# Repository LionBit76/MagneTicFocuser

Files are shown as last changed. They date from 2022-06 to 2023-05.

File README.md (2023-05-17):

# MagneTicFocuser [MTF]
DIY focuser for astrophotography with a magnetic flange

My Blogpost with more details (german): https://astrophoto.lionbit.com/3d-druck/22-magneticfocuser

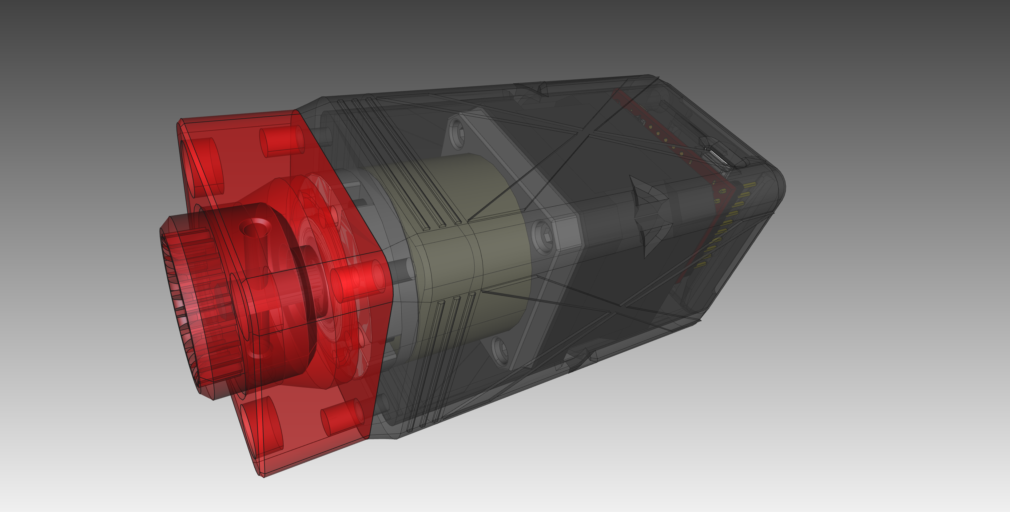
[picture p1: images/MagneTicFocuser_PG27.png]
This is an image


When I was looking for a cheap way to get a focuser, I came across a project on GitHub called TicFocuser-NG. This is an INDI driver for a Pololu TIC Controller. This controller is a small, compact circuit board with a stepper motor driver and a controller that is addressed via MicroUSB. The advantage of this solution is that you don't need an Arduino or Raspberry Pi to control the stepper motor driver, everything is on a board that is smaller than the area of a NEMA17 motor.

This focuser is for astrophotography with the INDI driver TicFocuser-ng https://github.com/sebo-b/TicFocuser-ng

### BOM [MagneTicFocuser]:

- 1x STEPPERONLINE 17HS13-0404S-PG27 
- 1x Pololu Tic T500 
- 4x M3x6 for fastening the geared motor 
- 4x M3x10 for the connection between housing and magnet plate
- 2x M2x8 self-tapping for attaching the controller
- 2x M4x10 grub screw for the clutch
- 4 N45 neodymium magnets 9x5 (4 more for the flange on the telescope)
- 1x barrel connector socket 5.5x2.1 for 12V DC
- 4x heatset inserts M3 5x6 (I have the VORON compatible heatset inserts)
- Superglue to stick the magnets in place
- JST connectors 4-pin for stepper, 2-pin for 12v

### Motor settings:
My settings in the Tic Software for the stepper motor are:
- Current limit: 1mA (yes, it works!)
- Step mode: 1/8 step (for maximum resolution and less vibrations on accel/deccel)
- Max speed: 8000000
- Max accel: 80000

### MagneTicFocuser and Explore Scientific ED80:
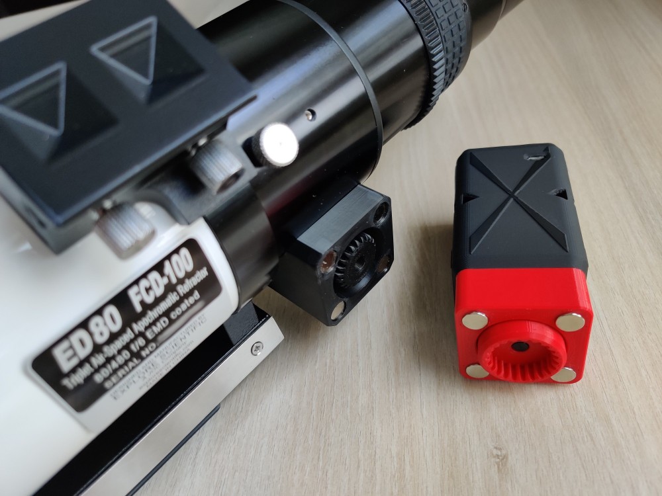
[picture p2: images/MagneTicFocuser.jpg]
This is an image


### MagneTicFocuser mounted on Explore Scientific ED80:
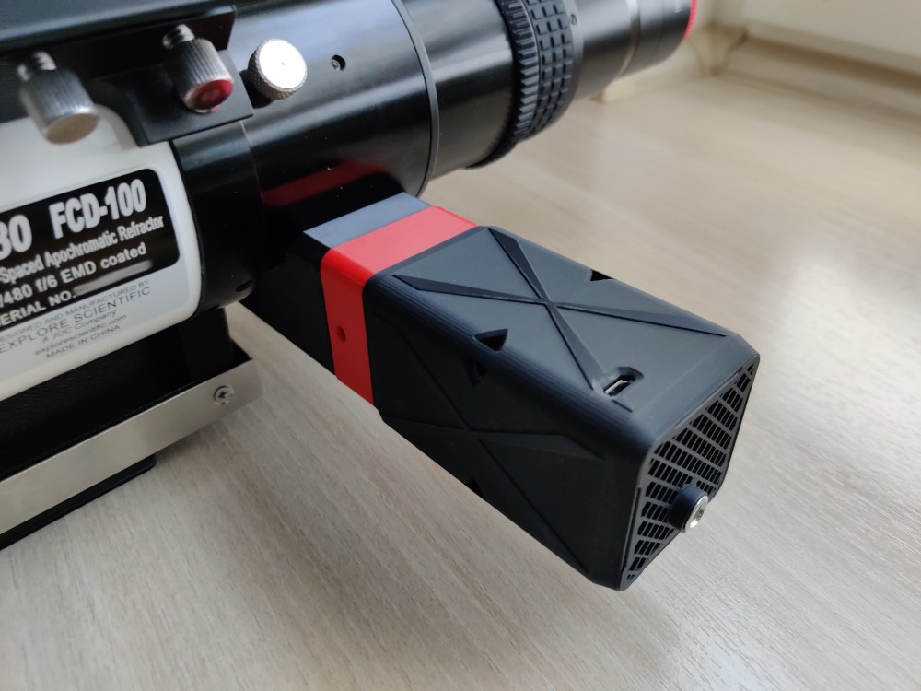
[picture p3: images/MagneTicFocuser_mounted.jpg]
This is an image


### MagneTicFocuser mounted on a Newton with Baader BDS-NT Focuser:
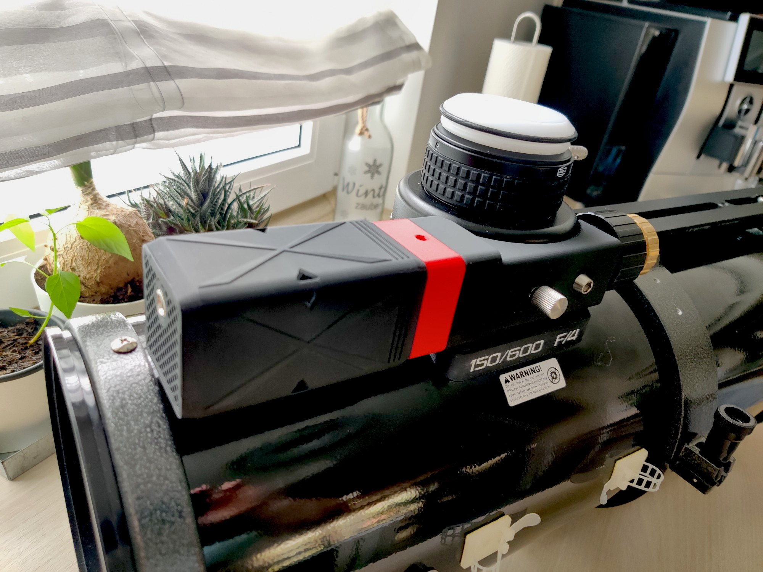
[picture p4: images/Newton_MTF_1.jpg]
This is an image

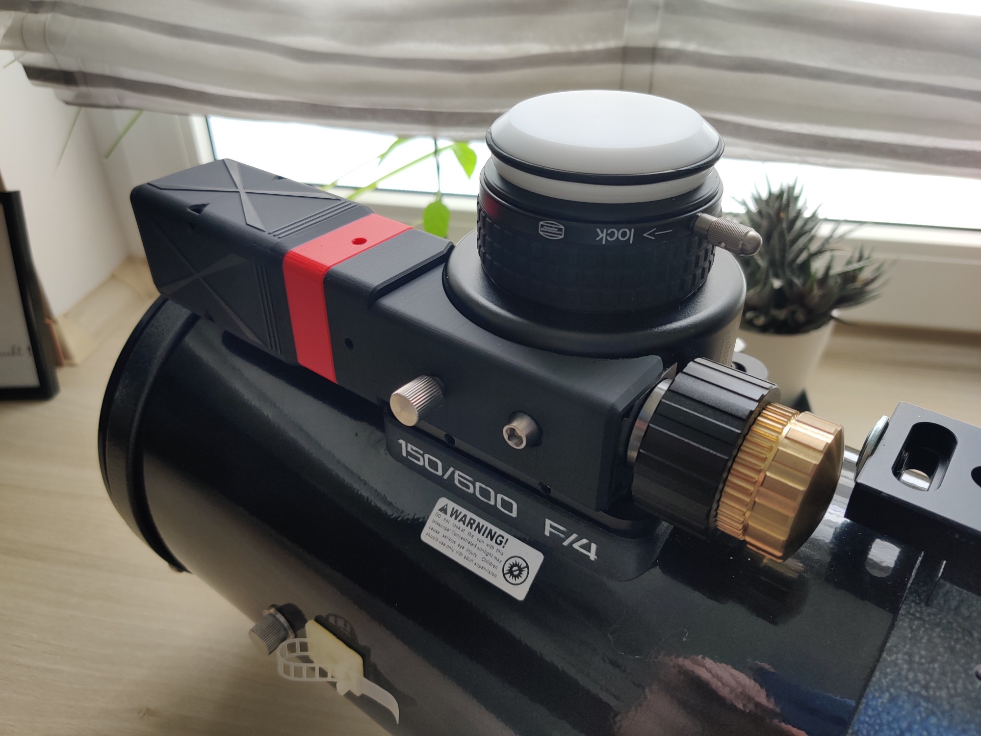
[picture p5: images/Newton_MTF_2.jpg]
This is an image


### My Rig:
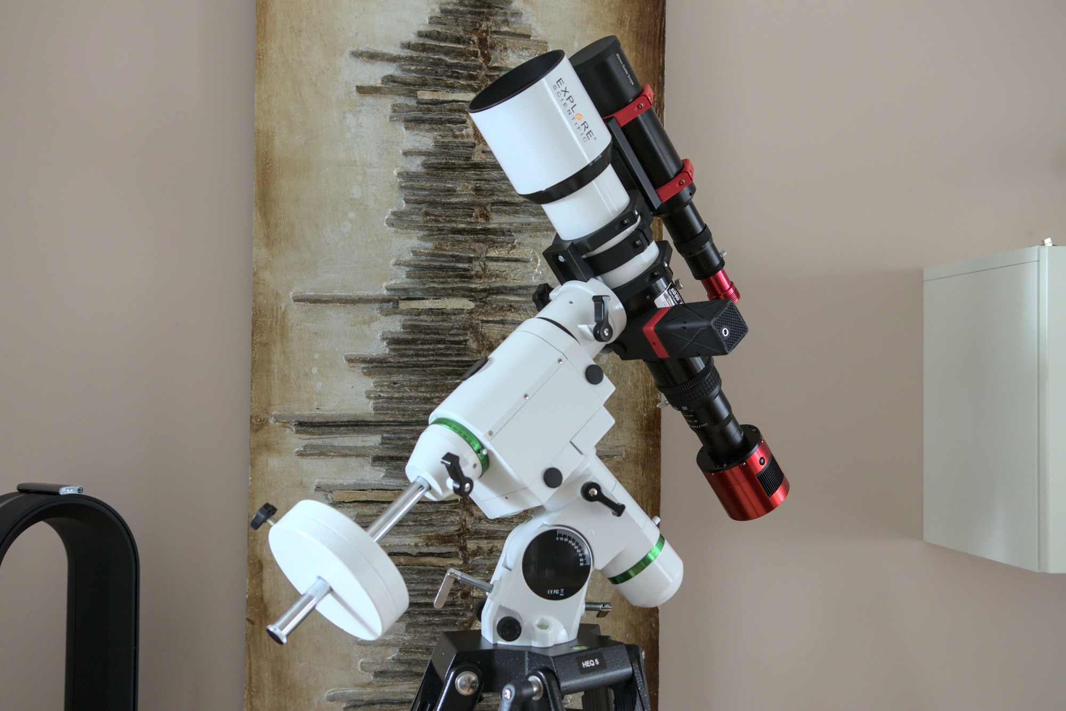
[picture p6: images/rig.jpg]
This is an image


### MTF to EAF Adapter:
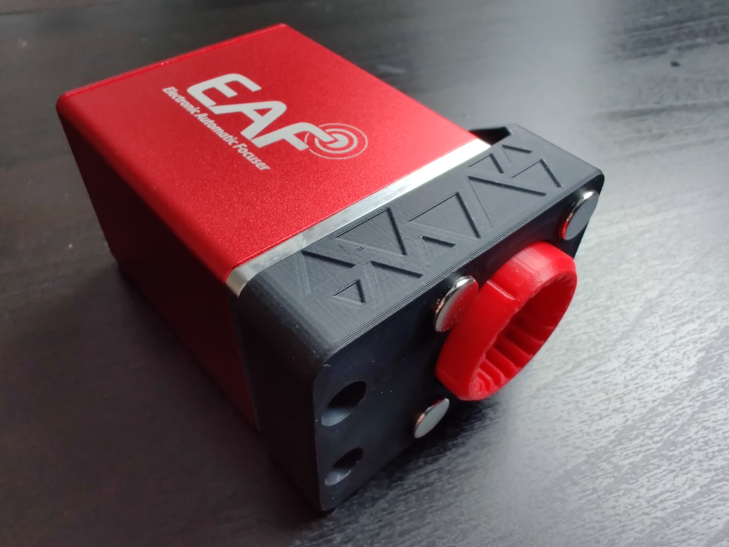
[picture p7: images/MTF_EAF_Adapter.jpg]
This is an image

If you have an ZWO EAF, you can adapt it to the MTF (MagneTicFocuser) System

### How to mount:
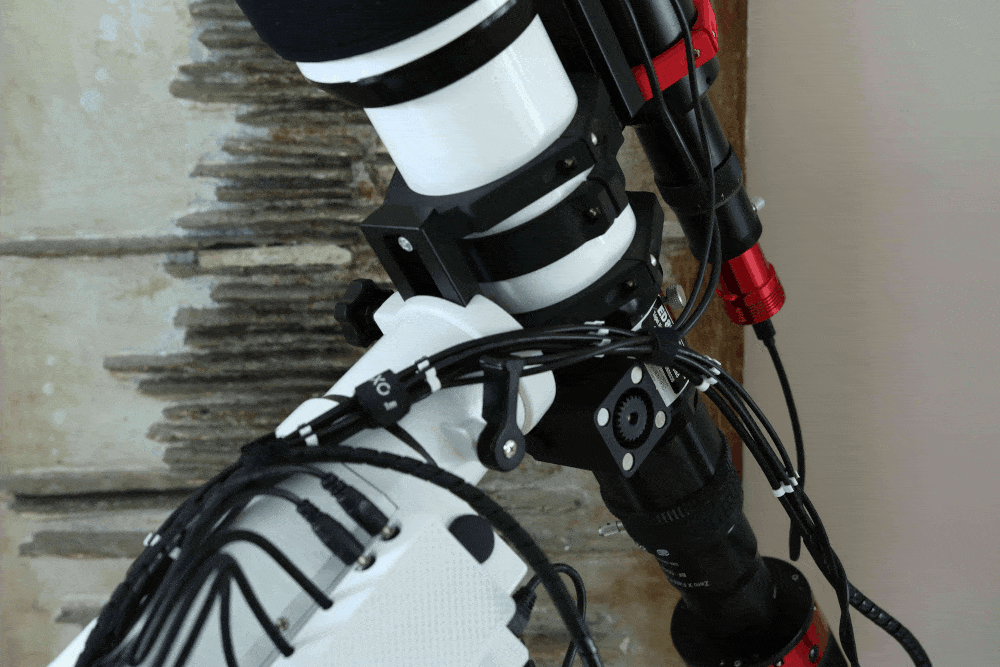
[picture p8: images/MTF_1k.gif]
This is an image


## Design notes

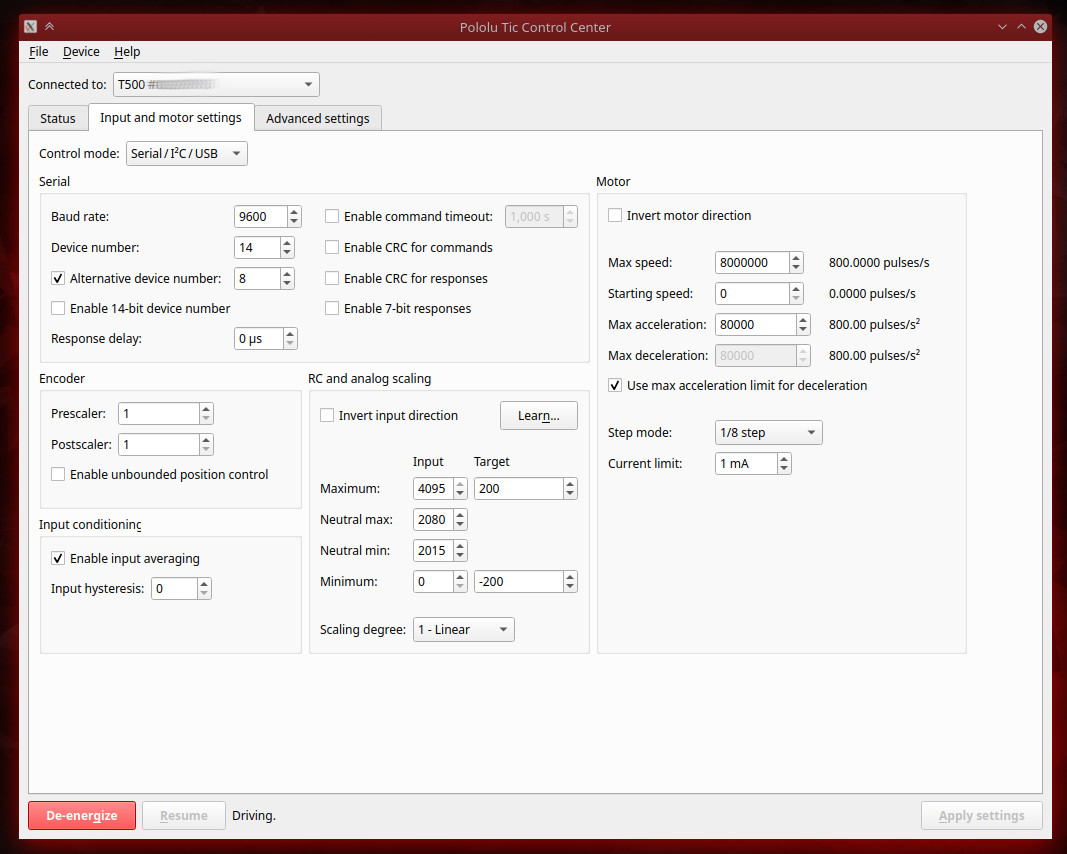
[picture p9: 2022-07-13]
images/TicGUI_Tab_InputMotorSetting.jpg

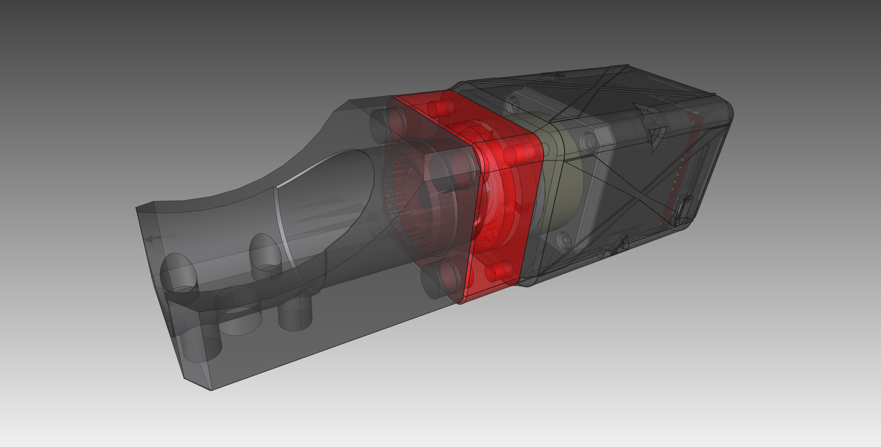
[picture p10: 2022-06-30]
images/MagneTicFocuser_ES_FCD100.png

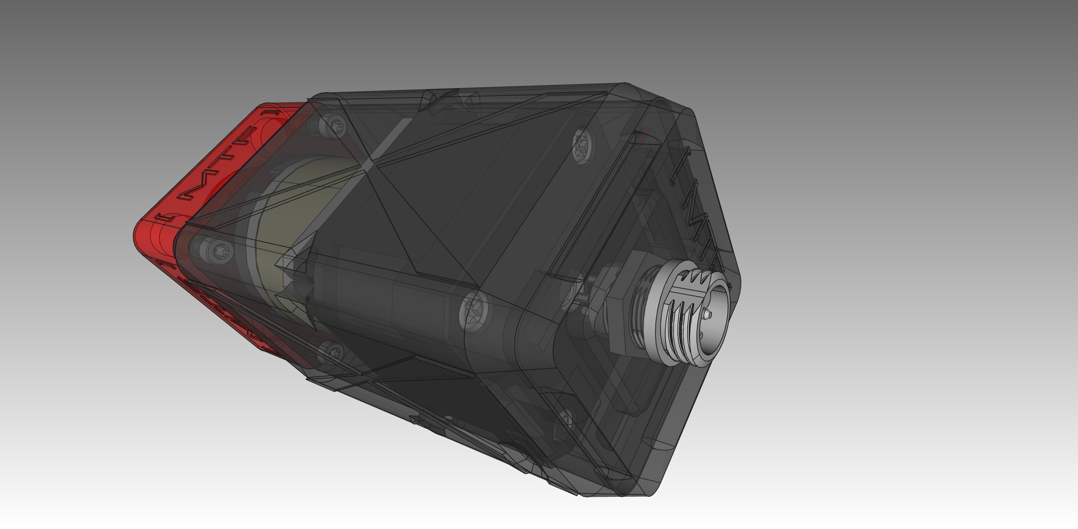
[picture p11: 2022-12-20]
STL/MTF-GX12/MTF_GX12_Back.png

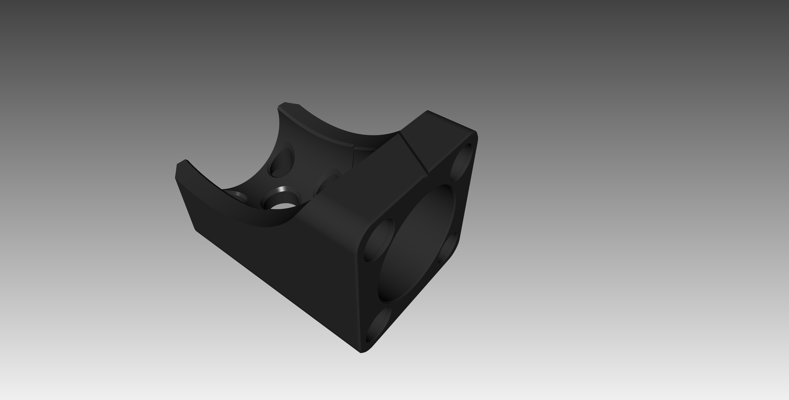
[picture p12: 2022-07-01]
STL/Telescope_Flange/Hexafoc/MTF_Hexafoc.png

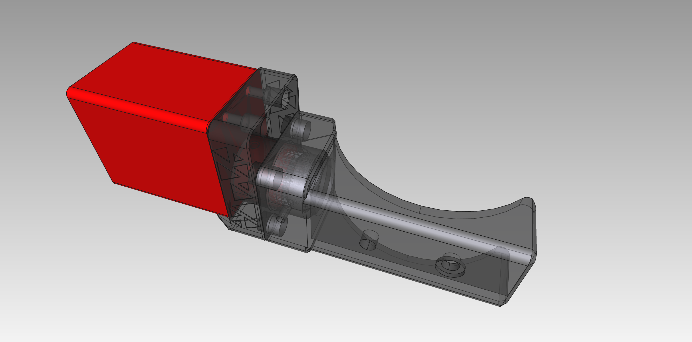
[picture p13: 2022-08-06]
STL/MTF_EAF/EAF_Adapter.png

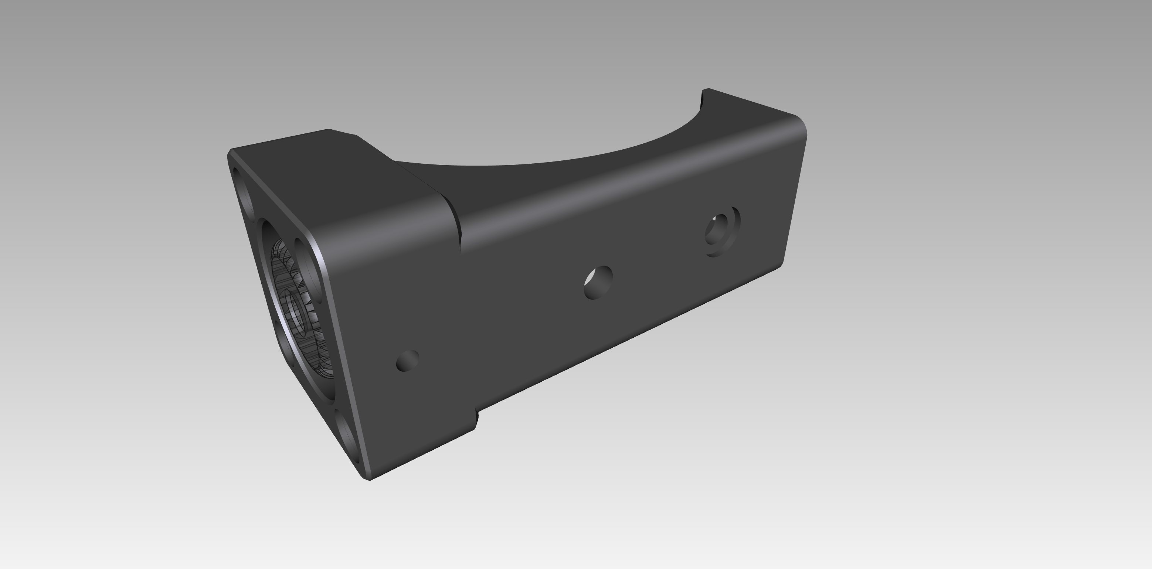
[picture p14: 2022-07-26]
STL/Telescope_Flange/Baader_BDS/MTF_BAADER_BDS.png

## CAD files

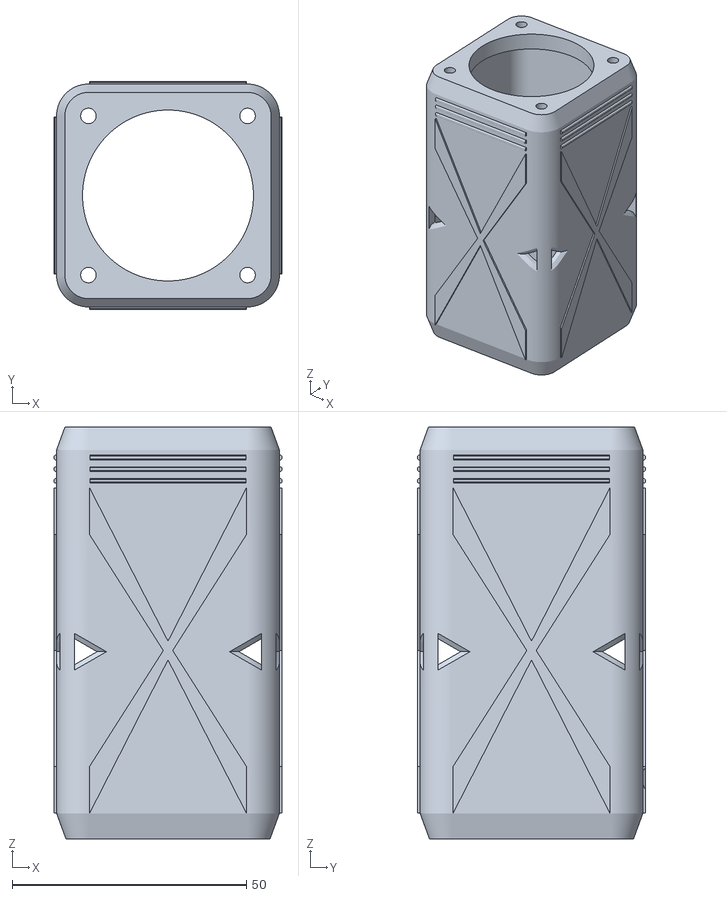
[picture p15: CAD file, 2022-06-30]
STL/MagneTicFocuser/MTF_Housing.stl
48.6 x 48.6 x 88.0

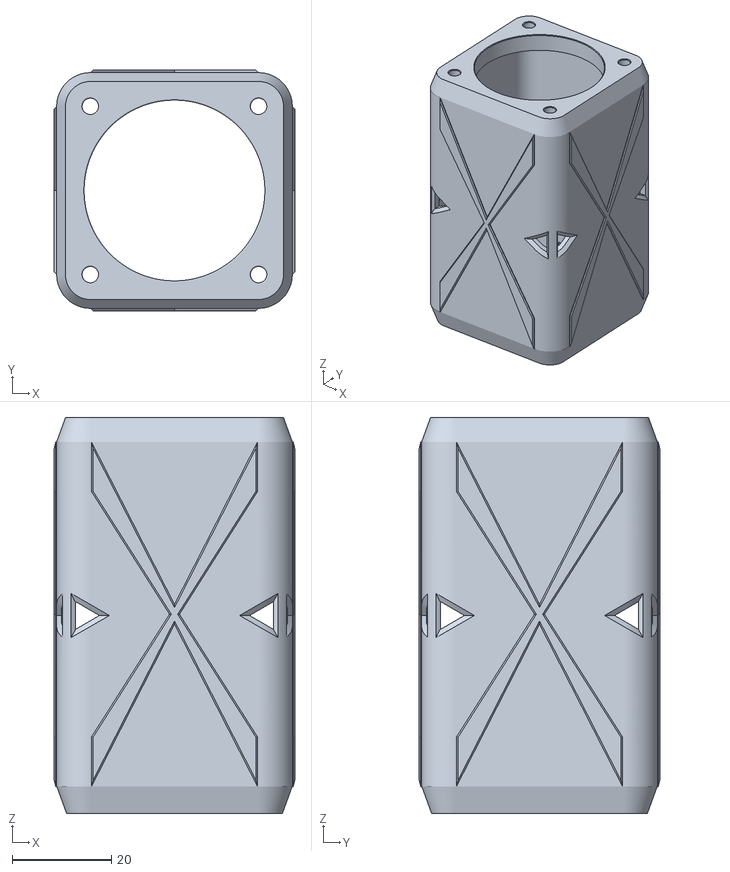
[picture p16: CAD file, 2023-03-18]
STL/MTF-GX12/MTF_Housing_PG5_GX12.stl
48.6 x 48.6 x 80.0

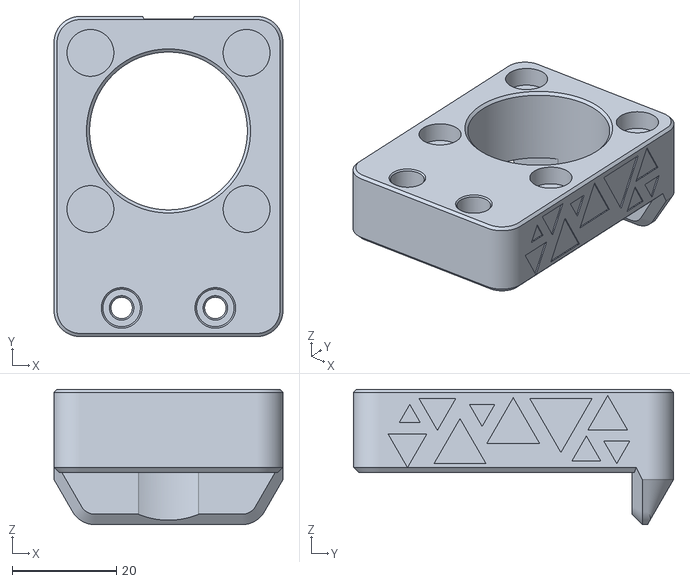
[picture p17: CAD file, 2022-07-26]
STL/MTF_EAF/EAF_Adapter.stl
44.0 x 61.5 x 26.0

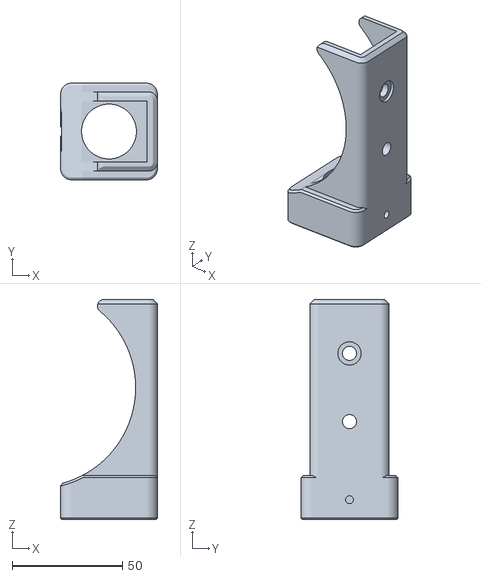
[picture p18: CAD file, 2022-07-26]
STL/Telescope_Flange/Baader_BDS/MTF_BAADER_BDS.stl
44.0 x 44.0 x 100.0

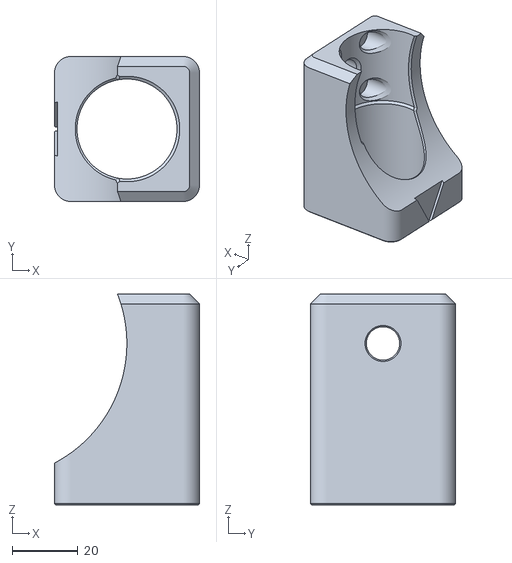
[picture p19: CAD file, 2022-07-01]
STL/Telescope_Flange/Hexafoc/MTF_Hexafoc.stl
44.0 x 44.0 x 64.0

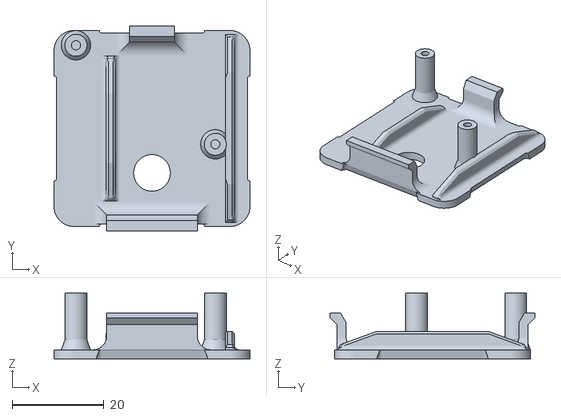
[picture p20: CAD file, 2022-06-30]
STL/MagneTicFocuser/MTF_Cover.stl
42.8 x 44.8 x 14.4

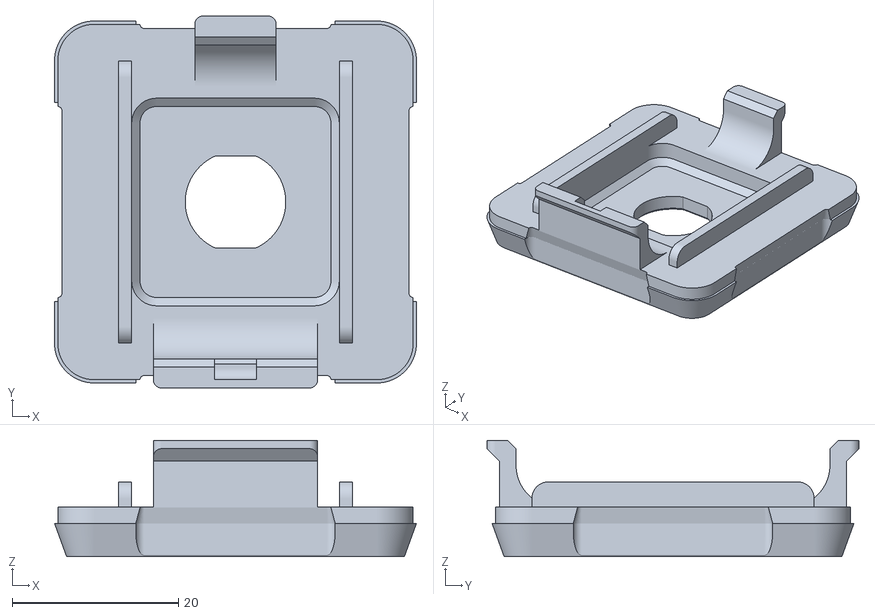
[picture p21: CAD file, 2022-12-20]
STL/MTF-GX12/MTF_Cover_GX12.stl
43.6 x 44.8 x 14.0

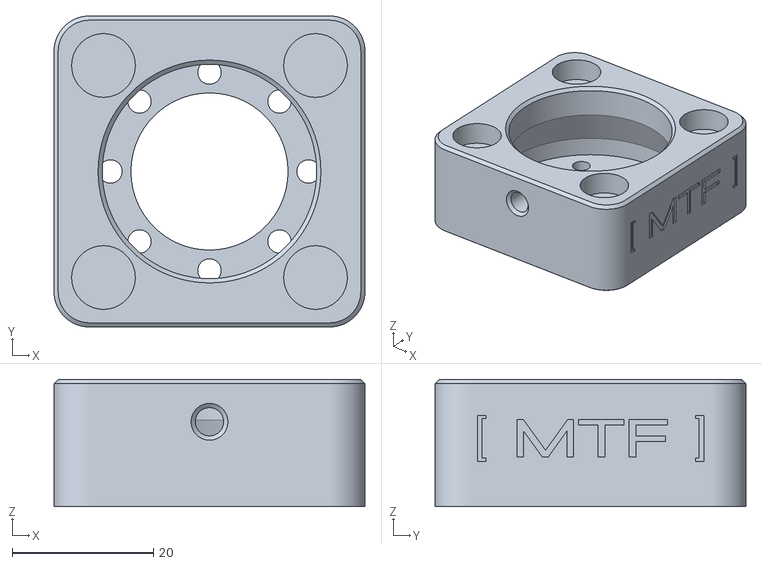
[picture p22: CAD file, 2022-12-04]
STL/MTF-GX12/MTF_Magnet_Plate.stl
44.0 x 44.0 x 18.0

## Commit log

2022-07-04 Update README.md
    added motor settings
2022-07-04 Update README.md
    updated motor settings
2022-07-09 Updated 12V socket
    Made the 12V socket flush with the surface
    [MTF_Cover.stl]
2022-07-26 Added Baader BDS Mount on a Newton
2022-12-04 Updated MTF_Magnet_Plate
    Added [MTF] engraving
    [MTF_Magnet_Plate.stl]
2022-12-20 Add files via upload
    A variant without electronics to use it with OnStep
    [MTF_Cover_GX12.stl, MTF_Housing_PG5.stl, MTF_Magnet_Plate.stl]
2022-12-20 Upated coupler to print without supports
2023-03-18 removed USB hole because it is not needed
    [MTF_Housing_PG5_GX12.stl]
